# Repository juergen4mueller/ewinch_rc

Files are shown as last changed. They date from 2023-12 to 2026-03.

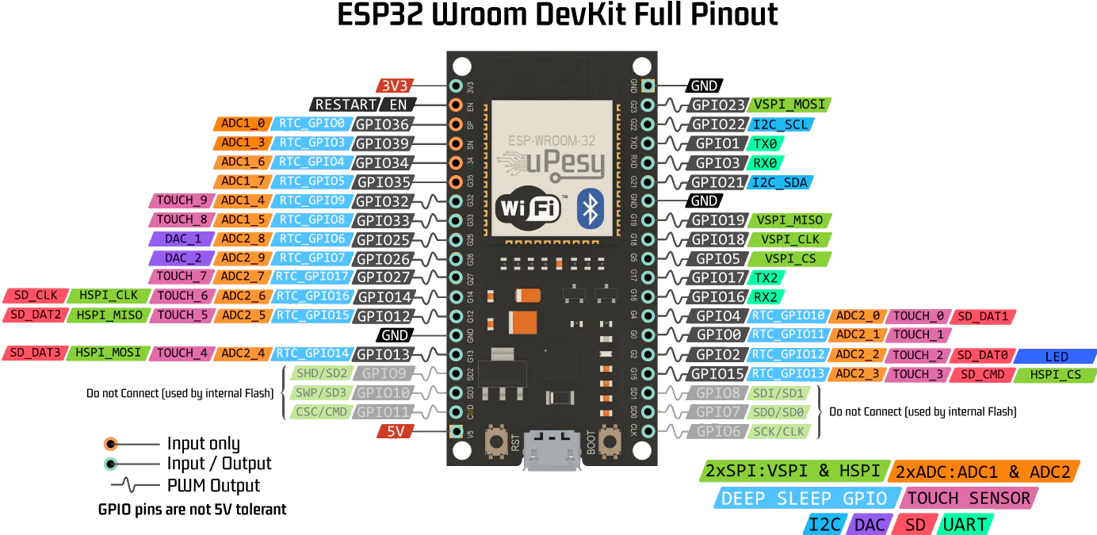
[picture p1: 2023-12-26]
doc/ESP32_38_Pinout.png

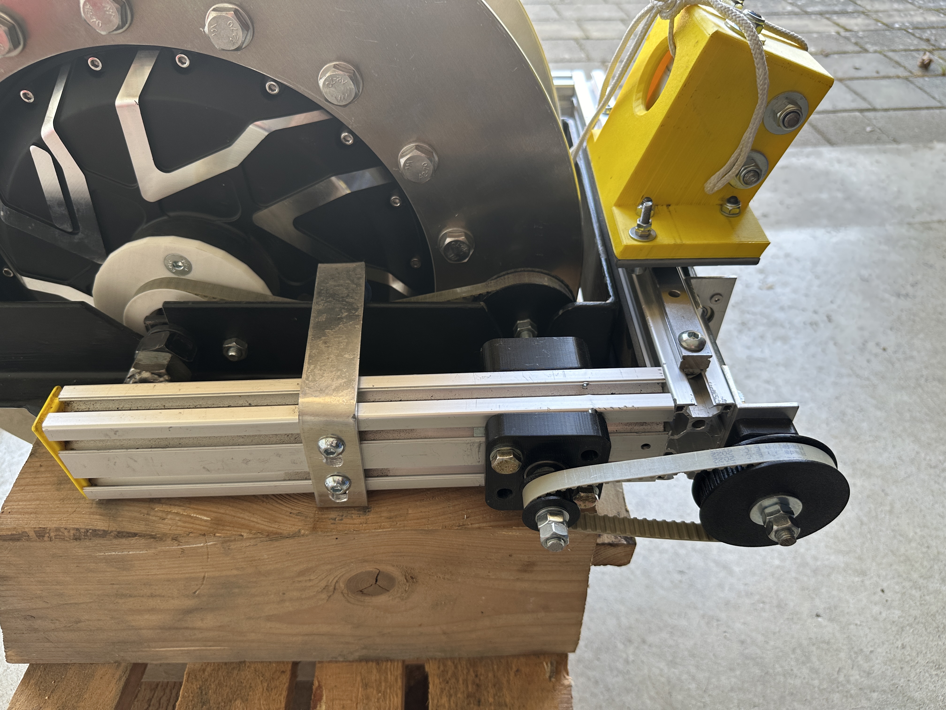
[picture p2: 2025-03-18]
doc/IMG_1781 2.JPG

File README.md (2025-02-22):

# ewinch_remote_controller
 transmitter and receiver code for remote controlling a paragliding winch
 forked from robertzach/ewinch_remote_controller

receiver uses PPM for driving the winch and (optinal) UART to read additional information (line length, battery %, dutycycle)
VESC UART communication depends on https://github.com/SolidGeek/VescUart/

Line auto stop can be implemented within VESC with vesc_ppm_auto_stop.patch
Default VESC app config is vesc_app_config.xml

## Changes / Updates
 Changed ESP32-Board to custom made with MH-ET-ESP32-Devkit and Heltec ESP32-Lora(v3).
 chandrawi/LoRaRF-lib for usage of SX126x modul on Heltec v3.
 Made new case for Heltec module, same size but different mount points.
 Moved software project to PLATFORMIO using VSCode for convenience work.

## Software improvements:
 - rotary encoder in transmitter to adjust max. weight, default pull and transmitter id (push while switch on, then select and push to confirm)
 - EEPROM function in transmitter to hold last "max. weight" value.
 - rotary encoder in receiver used to pull manually (adjust force by turning, push stops immediately)

## work in progress
 - wind direction from winch transmitting to cockpit display
 - warning lamp if pull mode active
 - cutting system

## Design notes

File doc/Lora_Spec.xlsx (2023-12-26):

Sx1272 |  |  | Sx1262
Lora Packet
Preamble | Sync, 12 Symbol long, Length variable (RegPreambleMsb, RegPreambleLsb)
Header / CRC | Nur verwendet wenn RegModemConfig1:ImplicitHeaderModeOn gesetzt ist
Expl. Header Mode | Ist default mode: Payload Length, ECCR, CRC?
Impl. Header Mode | Wenn SF (spreading factor) == 6 nur impl. Header mode möglich
Payload | Daten
CRC
Spreading Factor | RegModemConfig2 (6 für highest data rate)
Coding Rate | RegModemConfig1
Bandwidth
Mode | RXCONTINUOUS
SyncWord | default: 0xF5 | MSB:0x14, LSB:0x24
PreambleSize | def: 0x00
RegOpMode(0x01) | def:0x00 LoRa:0x80 , ModeSTBY:0x01, ModeTX:0x03, ModeRXSINGLE:0x6, ModeRXCONTINUOUS:0x5
RegModemConfig1(0x1D) | Bandwidth, CodingRate, ImplHeaderMode, RxPayloadCrcOn, LowDataRateOptimize
RegModemConfig2(0x1E) | SpreadingFaktor, TxContinuousMode, AgcAutoOn, SymbTimeout
RxGain |  | 0x94(PowerSaving), 0x96(Boost)
 |  | BUSY-Line: If Busy == 0, state machine waits for command
 |  | BUSY geht auch high wenn ein IRQ kommt. Dann erst die Daten lesen wenn BUSY wieder low ist
Packet Filtering based on preamble start

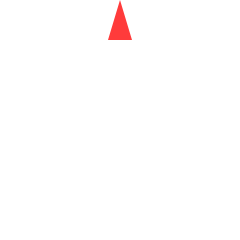
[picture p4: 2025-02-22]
assets/WindPfeil_2.png

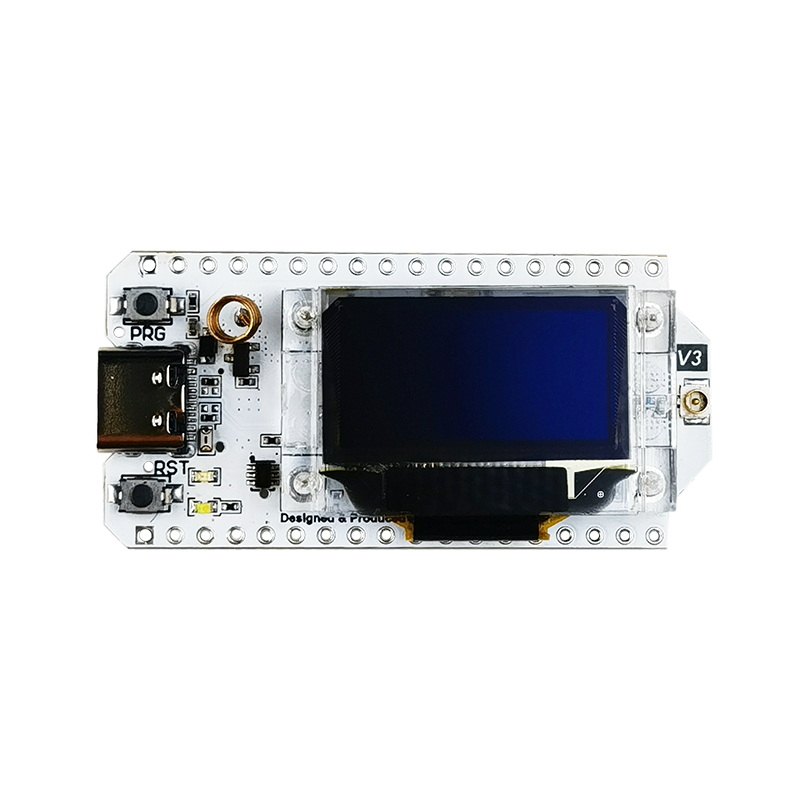
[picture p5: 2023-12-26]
doc/LORA32-V3vt.png

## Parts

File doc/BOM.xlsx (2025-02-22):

Bauteilliste Winde
QS Motors | 979.00 € | +Steuer
MakerX Go FOC G300 | 350.00 €
Trommelscheiben (Lasercut) | 150.00 €
Schrauben M12x150 + Muttern/Scheiben | 60.00 €
Stahlwinkel 80x80x6 | 16.14 €
Stahlwinkel 60x30x5 2m | 14.82 €
Stahlrohr 33,7x2,5 | 3.60 €
Stahlrohr 42,4x3,2 | 5.40 €
Alu-Rohr 30x2 | 11.79 €
Kugellager 10x26x8 | 7.90 €
Mutter M22x1,5 5St. | 8.45 €
Item 30x60 500mm 4St | 36.40 €
Kugellager 8x22x7mm | 10.00 €
Klappstecker 8x50mm | 10.00 €
Lenkungsdämpfer einstellbar | 150.00 €
Schleppseil 1040m 2,5mm | 345.00 €
Gewindestange M8
Alu-Winkel 30x30x3mm
Zahnriemen 10-T5/630 | 16.97 €
Zahnriemen 10-T5/350 | 16.20 €
Seilfallschirm
Sollbruchstelle
AliExpress
ESP32 SX1262 2x | 36.90 €
280x240x130mm Werkzeug kasten | 17.35 € | https://de.aliexpress.com/item/1005005539521602.html
Taster für Remote | 5.00 € | https://de.aliexpress.com/item/1005003256497233.html
Linearführung MGN15 H, China, 300mm | 16.86 € | https://de.aliexpress.com/item/32806622073.html
ESP32 Dev Modul 38P | 3.28 € | https://de.aliexpress.com/item/1005001636295529.html
KFL000 10mm Lager |  | https://de.aliexpress.com/item/1005002394517514.html
1,28" Display Remote | 17.00 € | https://www.waveshare.com/esp32-s3-lcd-1.28.htm
LiPo-Akkus LP603449 1100 mAh | 20.00 €
Diverse Schrauben …
Item-Nutensteine
3D-Druck-Teile
Lagersitz
Akku 72V/30Ah | 1000.00 €
Gesamtkosten | 3308.06 €

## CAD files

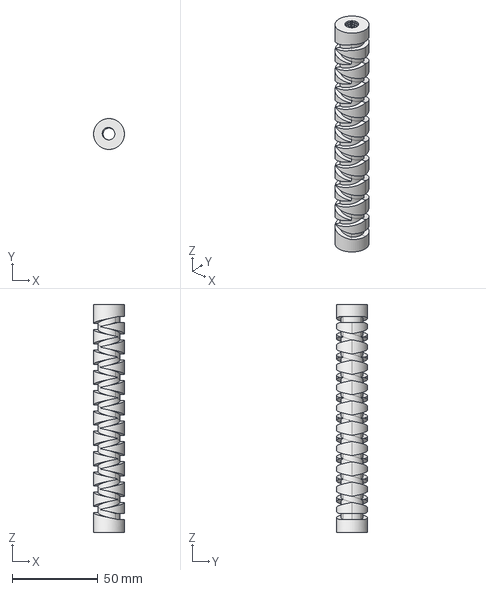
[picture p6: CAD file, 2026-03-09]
CAD/Kreuzspindel_kurz.step
18.0 x 18.0 x 133.0 mm

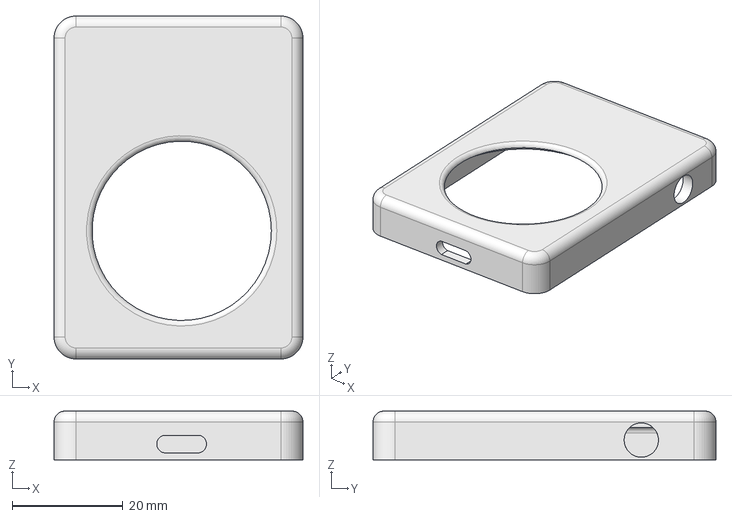
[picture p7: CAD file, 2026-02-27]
CockpitDisplay/DisplayCaseFront.step
45.0 x 62.0 x 8.85 mm

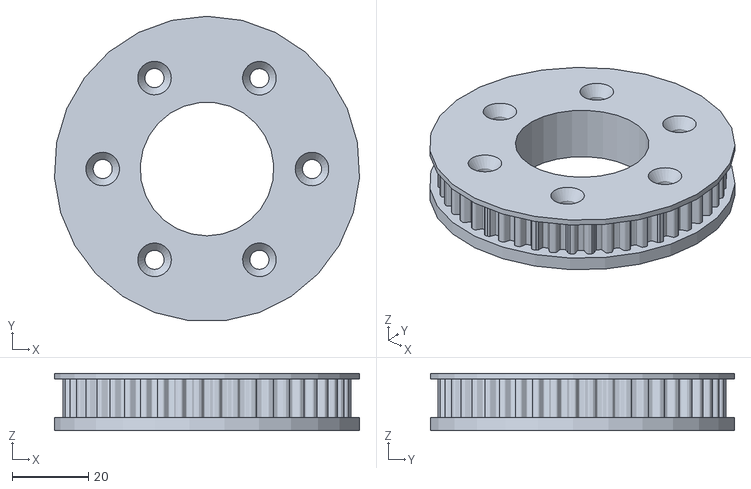
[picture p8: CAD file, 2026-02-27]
stl/belt_drive_B.stl
79.9 x 79.7 x 15.0

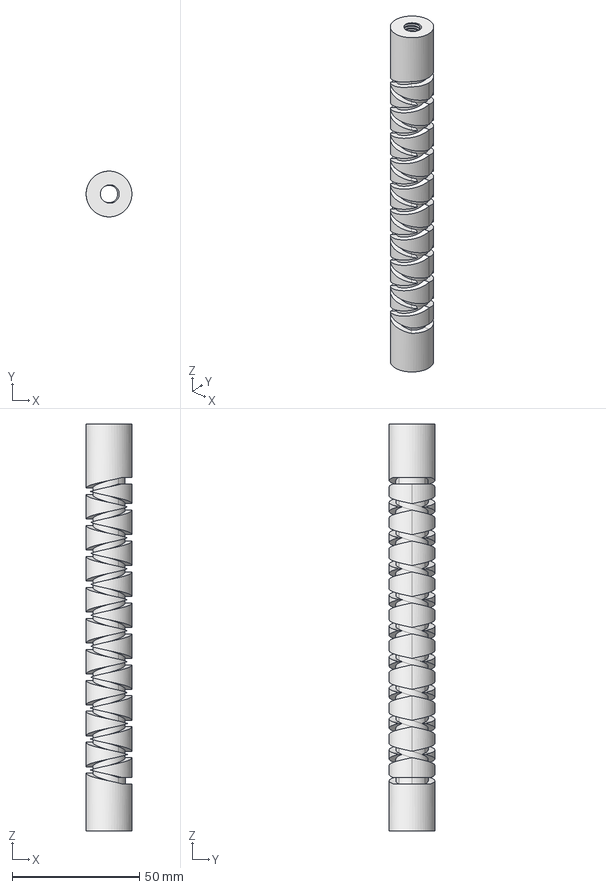
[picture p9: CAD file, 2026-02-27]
CAD/Kreuzspindel-slim_2.6_tief_10Gang.step
18.0 x 18.0 x 160.0 mm

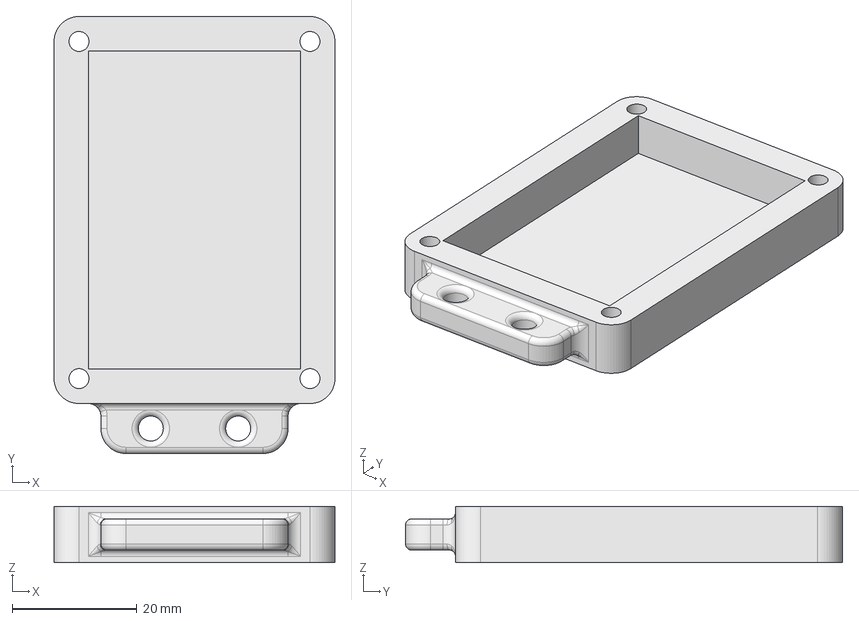
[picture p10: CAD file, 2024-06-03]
CockpitDisplay/DisplayCaseBack.step
45.0 x 70.0 x 9.00 mm

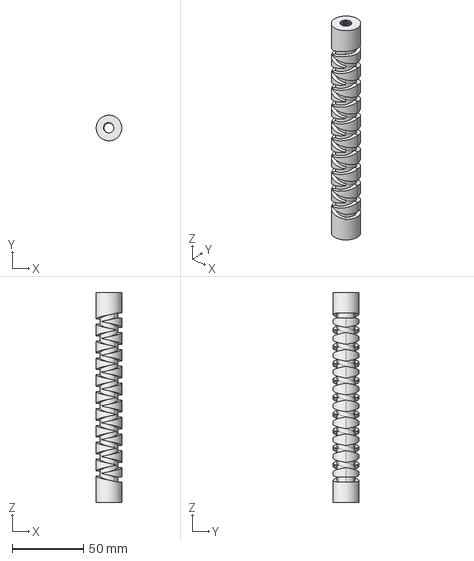
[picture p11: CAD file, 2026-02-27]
doc/CAD/Kreuzspindel_v2.step
18.0 x 18.0 x 147.5 mm

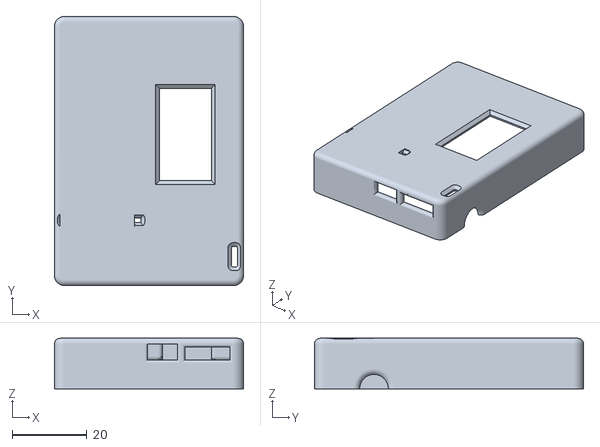
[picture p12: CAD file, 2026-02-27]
stl/transmitter_top.stl
50.6 x 71.9 x 13.5

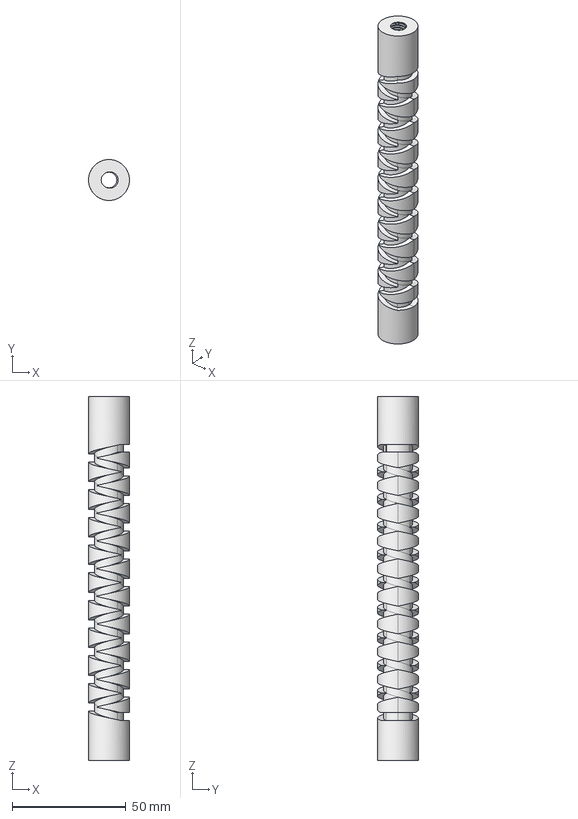
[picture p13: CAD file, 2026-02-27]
CAD/Kreuzspindel-Spindel_2.6_tief_10Gang.step
18.0 x 18.0 x 160.0 mm

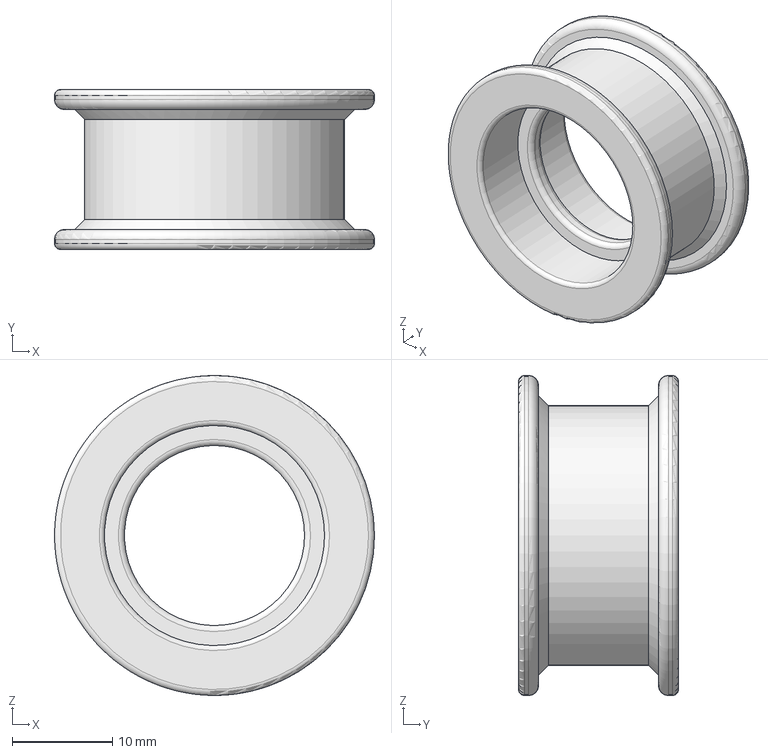
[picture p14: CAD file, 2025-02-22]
doc/CAD/Riemenspanner_Rolle.step
32.0 x 16.0 x 32.0 mm

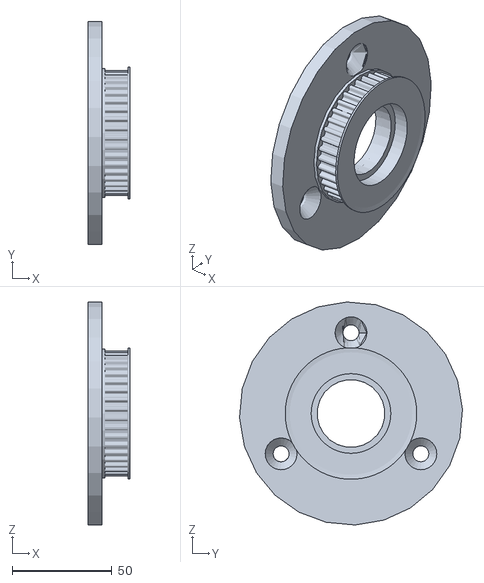
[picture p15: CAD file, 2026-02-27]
stl/belt_drive_A.stl
21.3 x 111.9 x 111.9

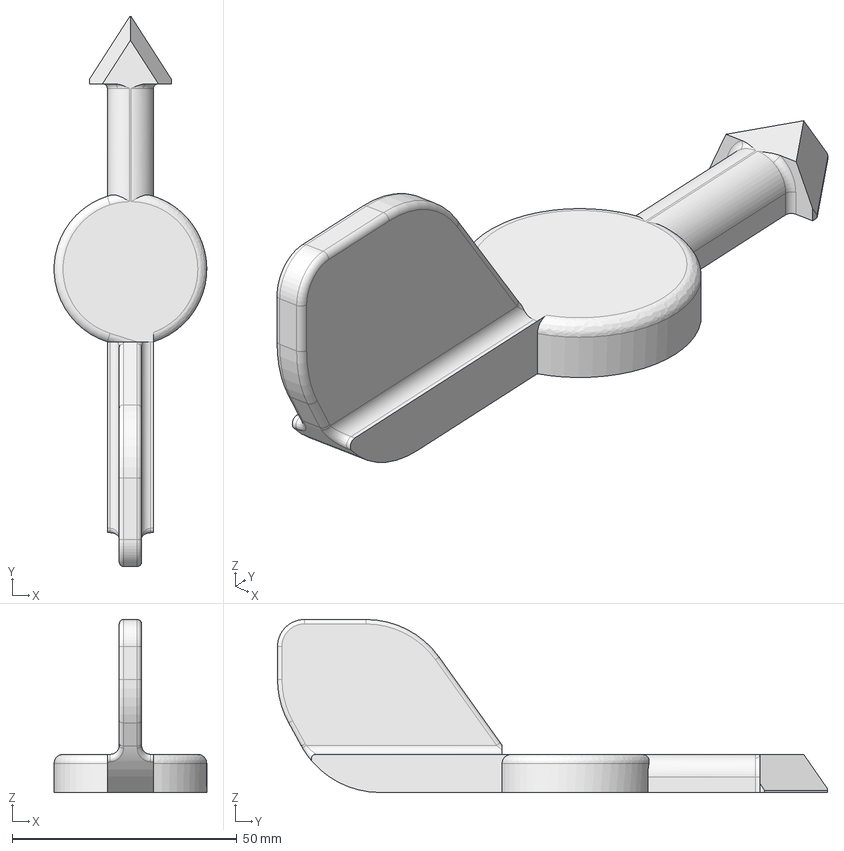
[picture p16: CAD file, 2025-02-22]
CAD/Windmesser.FCStd
34.0 x 122.4 x 38.5 mm

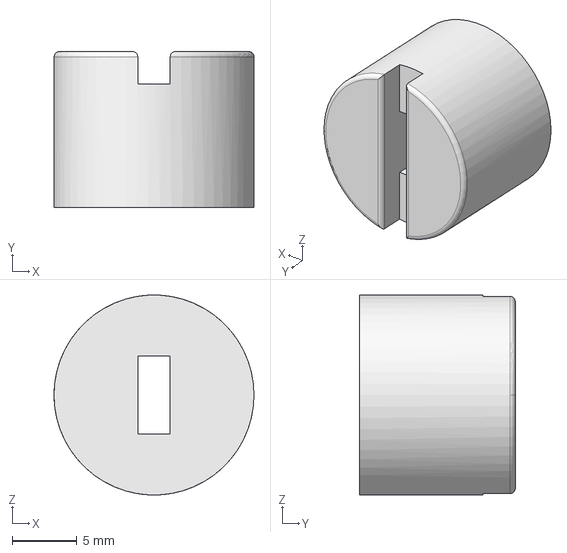
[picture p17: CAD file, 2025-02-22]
doc/CAD/Schleifersitz_Kreuzspindel.step
15.4 x 12.0 x 15.4 mm

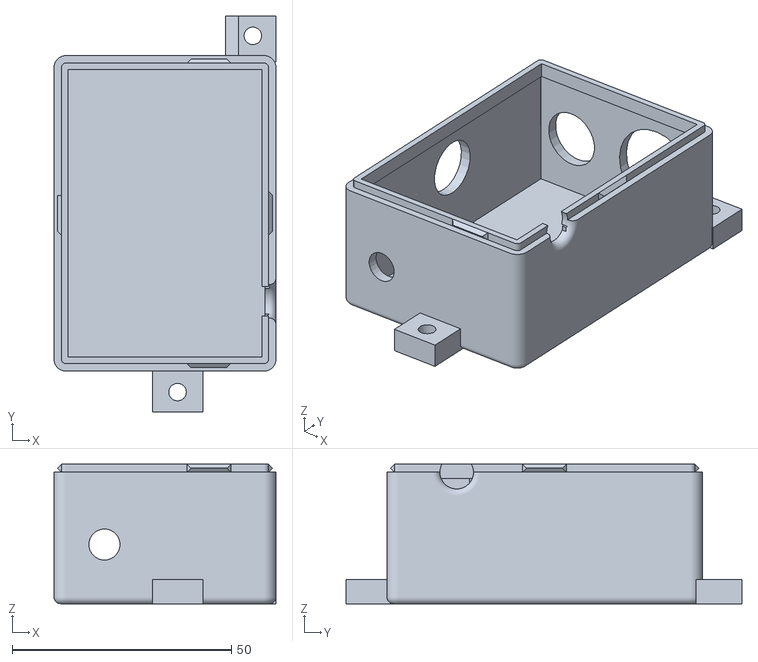
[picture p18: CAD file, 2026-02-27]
stl/transmitter_bottom.stl
50.6 x 90.2 x 31.8

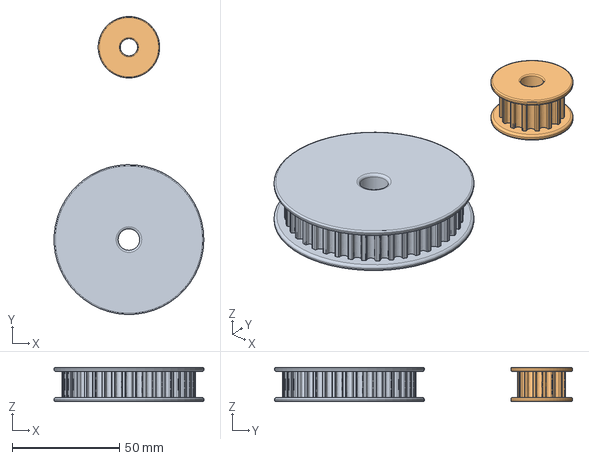
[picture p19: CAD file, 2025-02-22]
CAD/Riemenscheiben.FCStd
69.9 x 139.1 x 16.0 mm
40Z
15Z

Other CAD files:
doc/CAD/Remote_Display_Front.step
doc/CAD/Halter_Lagersitz_Spulvorrichtung.step
stl/TransmitterCaseHeltec_btm.stl
CAD/Halter_Spuler-Schablone.step
CAD/Halter_Spuler-Schablone2.step
CAD/Halter_Spuler.FCStd
CAD/LagerUmsetzer.FCStd
CAD/Riemenscheibe_40Z.FCStd
CAD/TransmCaseHeltec.FCStd
CAD/Trommelblatt_5mm_Alu.dxf
CAD/Winde_Trommelblatt.FCStd
doc/CAD/Gleiter_Kreuzspindel.step
doc/CAD/Gleiteradapter_Kreuzspindel.step
doc/CAD/LagerUmsetzer-Aussen15mm.step
doc/CAD/LagerUmsetzer-Innen25mm.step
doc/CAD/Lagersitz_Spulvorrichtung.step
doc/CAD/Remote_Display_Back.step
doc/CAD/Riemenscheibe_15Z.step
doc/CAD/Riemenscheibe_40Z.step
doc/CAD/Schleifer_Kreuzspindel.step
doc/CAD/Trommelblatt.step
doc/CAD/Trommelblatt_5mm_Alu.dxf
stl/TransmitterCaseHeltec_top.stl

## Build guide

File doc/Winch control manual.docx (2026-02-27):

Winch control manual

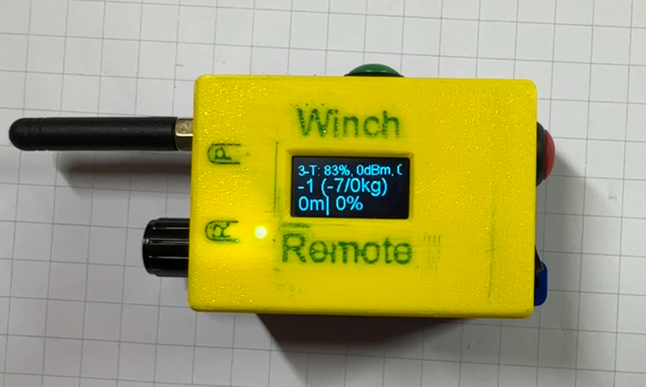
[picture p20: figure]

BTN UP

BTN DOWN

Setup Switch

Lora Antenna

Switch

ON / OFF

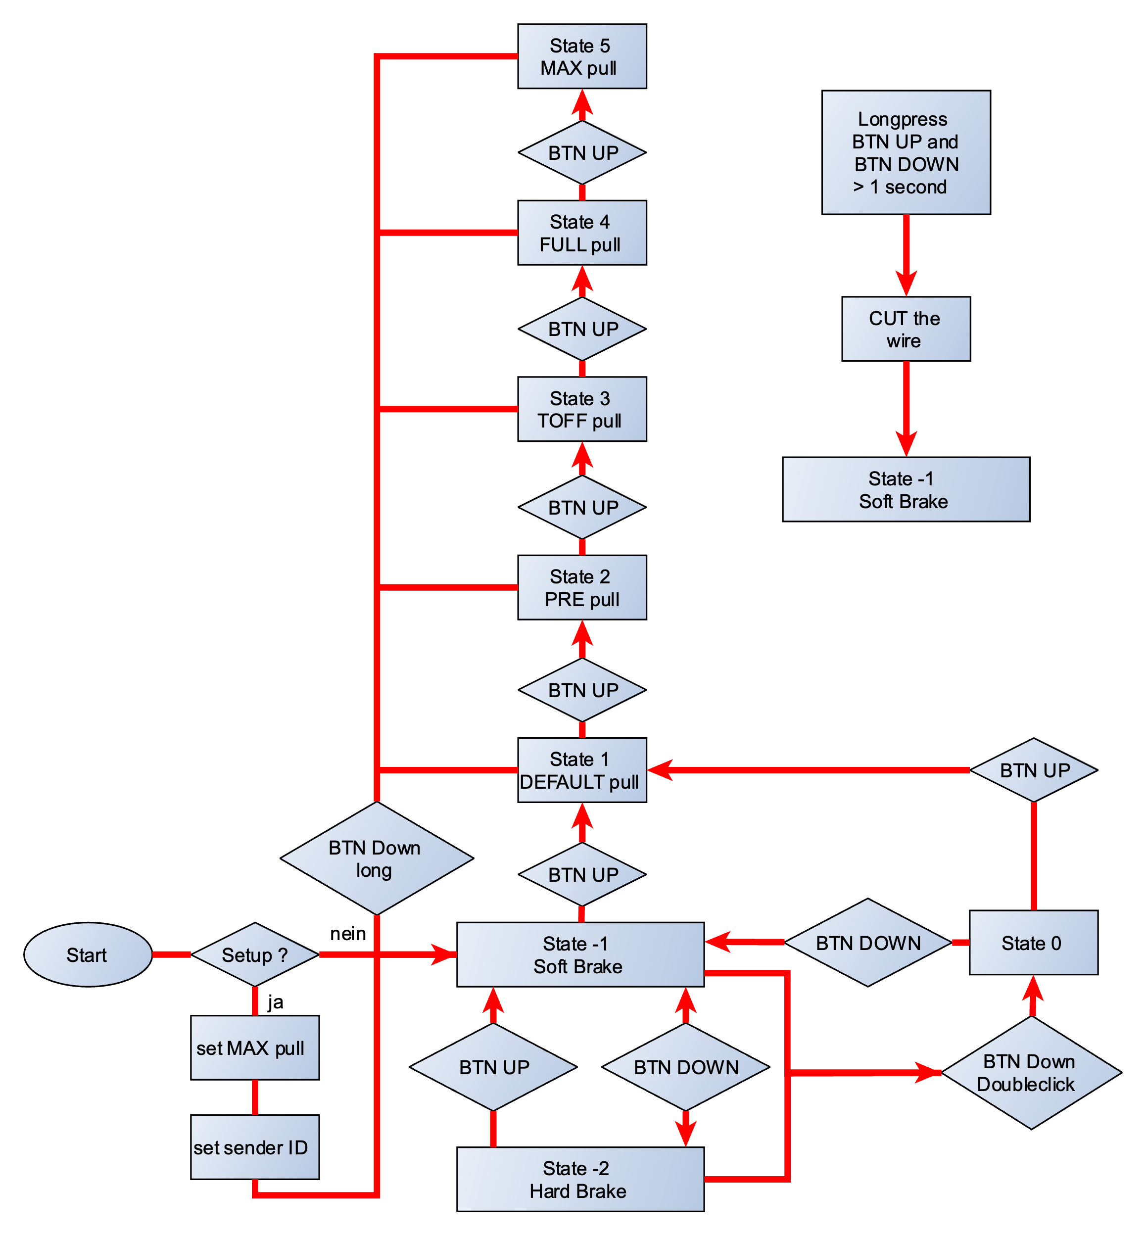
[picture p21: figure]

Remote Display

Due to the fact that the display on the remote control is hard to read while towing I made a display connected by ESP-NOW to the remote control.

This can be attached to the cockpit and is easy to read.

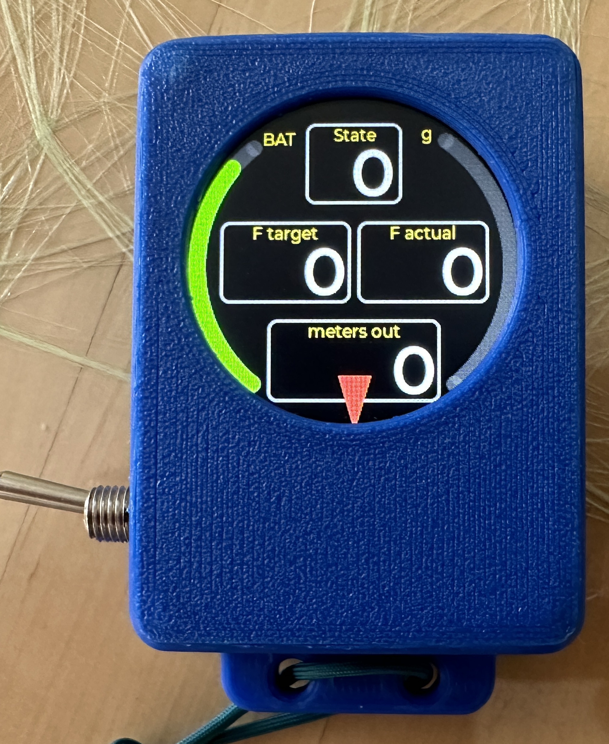
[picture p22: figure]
Remote Display Extention

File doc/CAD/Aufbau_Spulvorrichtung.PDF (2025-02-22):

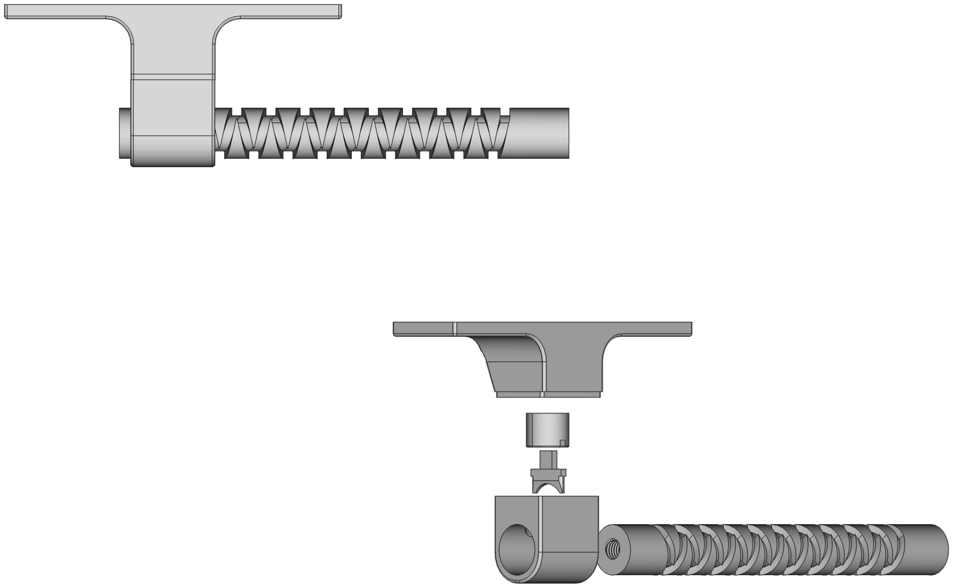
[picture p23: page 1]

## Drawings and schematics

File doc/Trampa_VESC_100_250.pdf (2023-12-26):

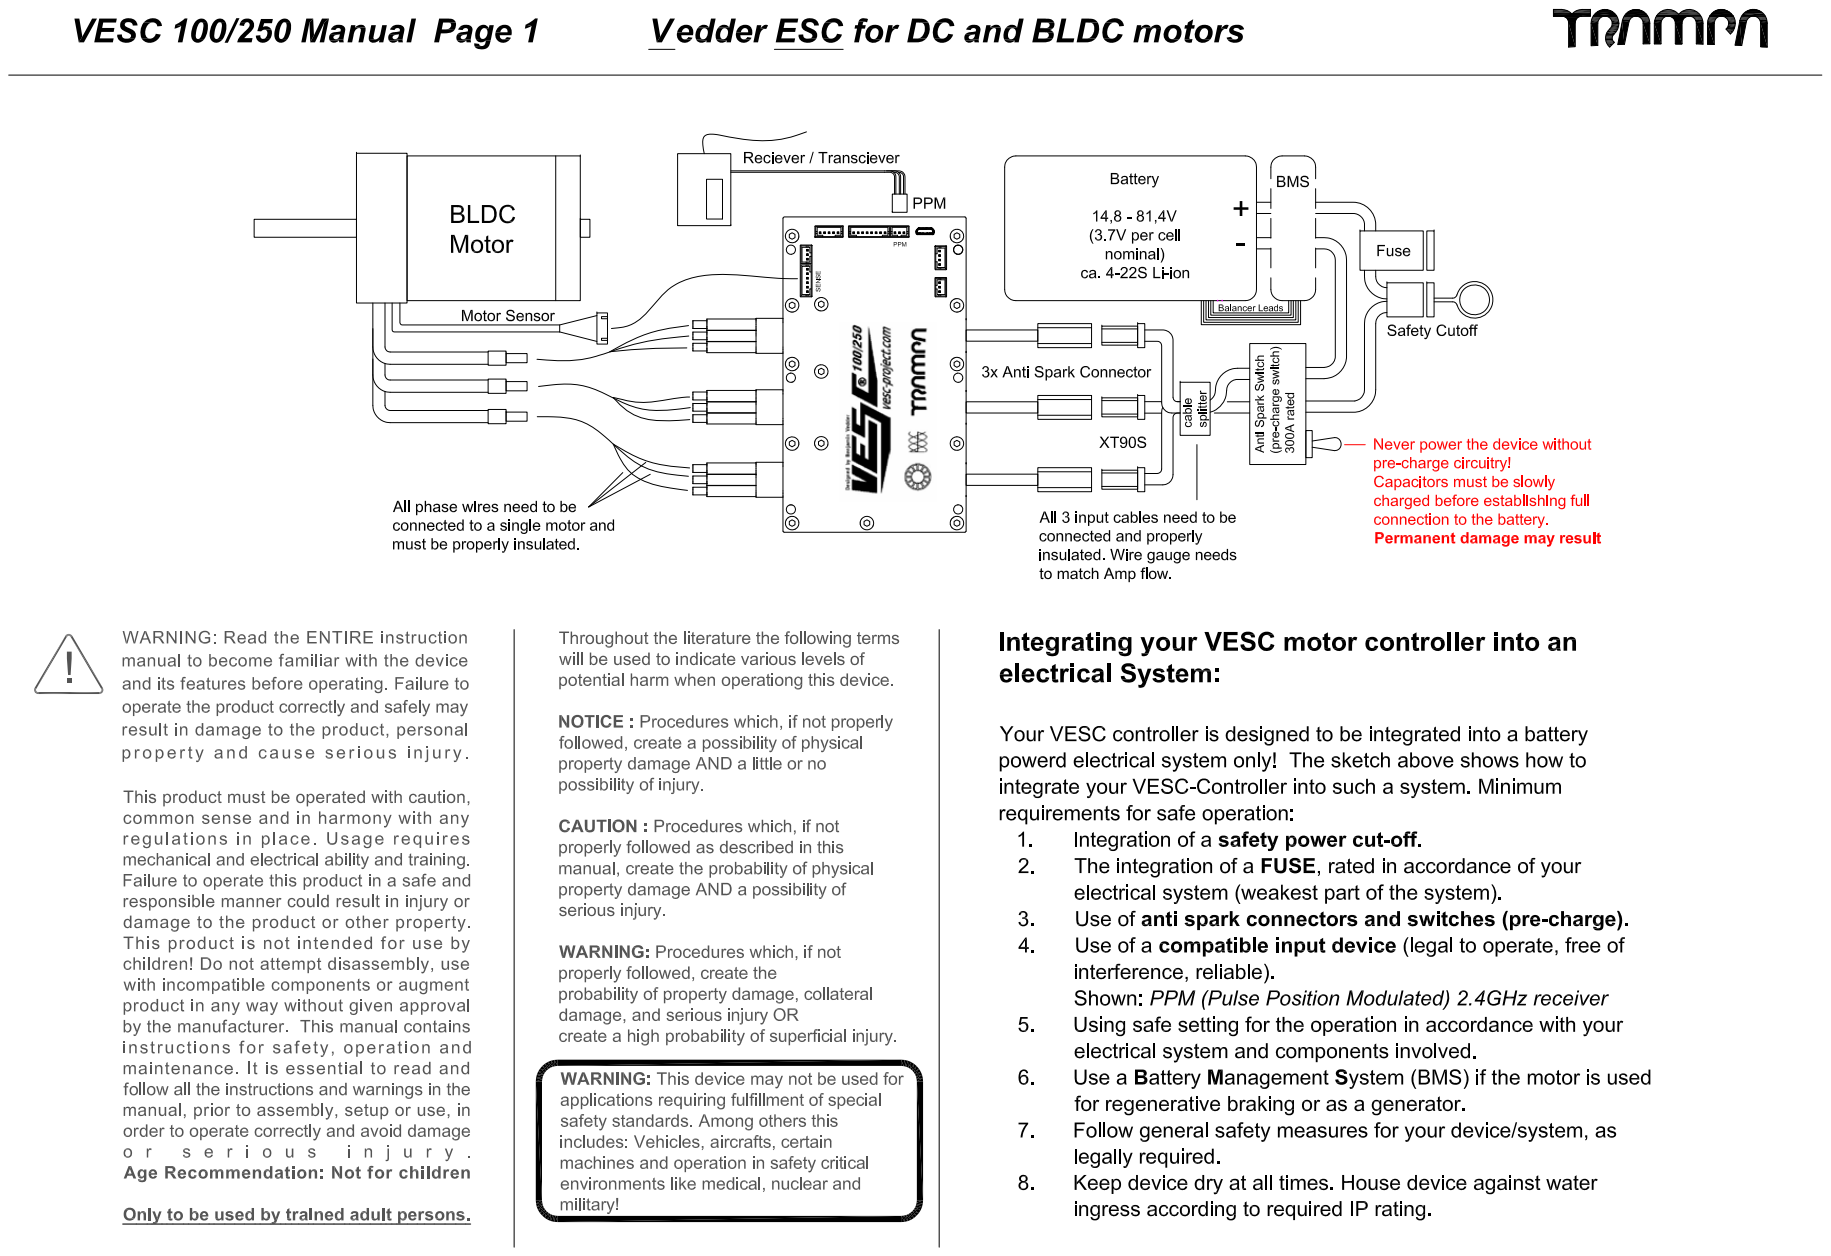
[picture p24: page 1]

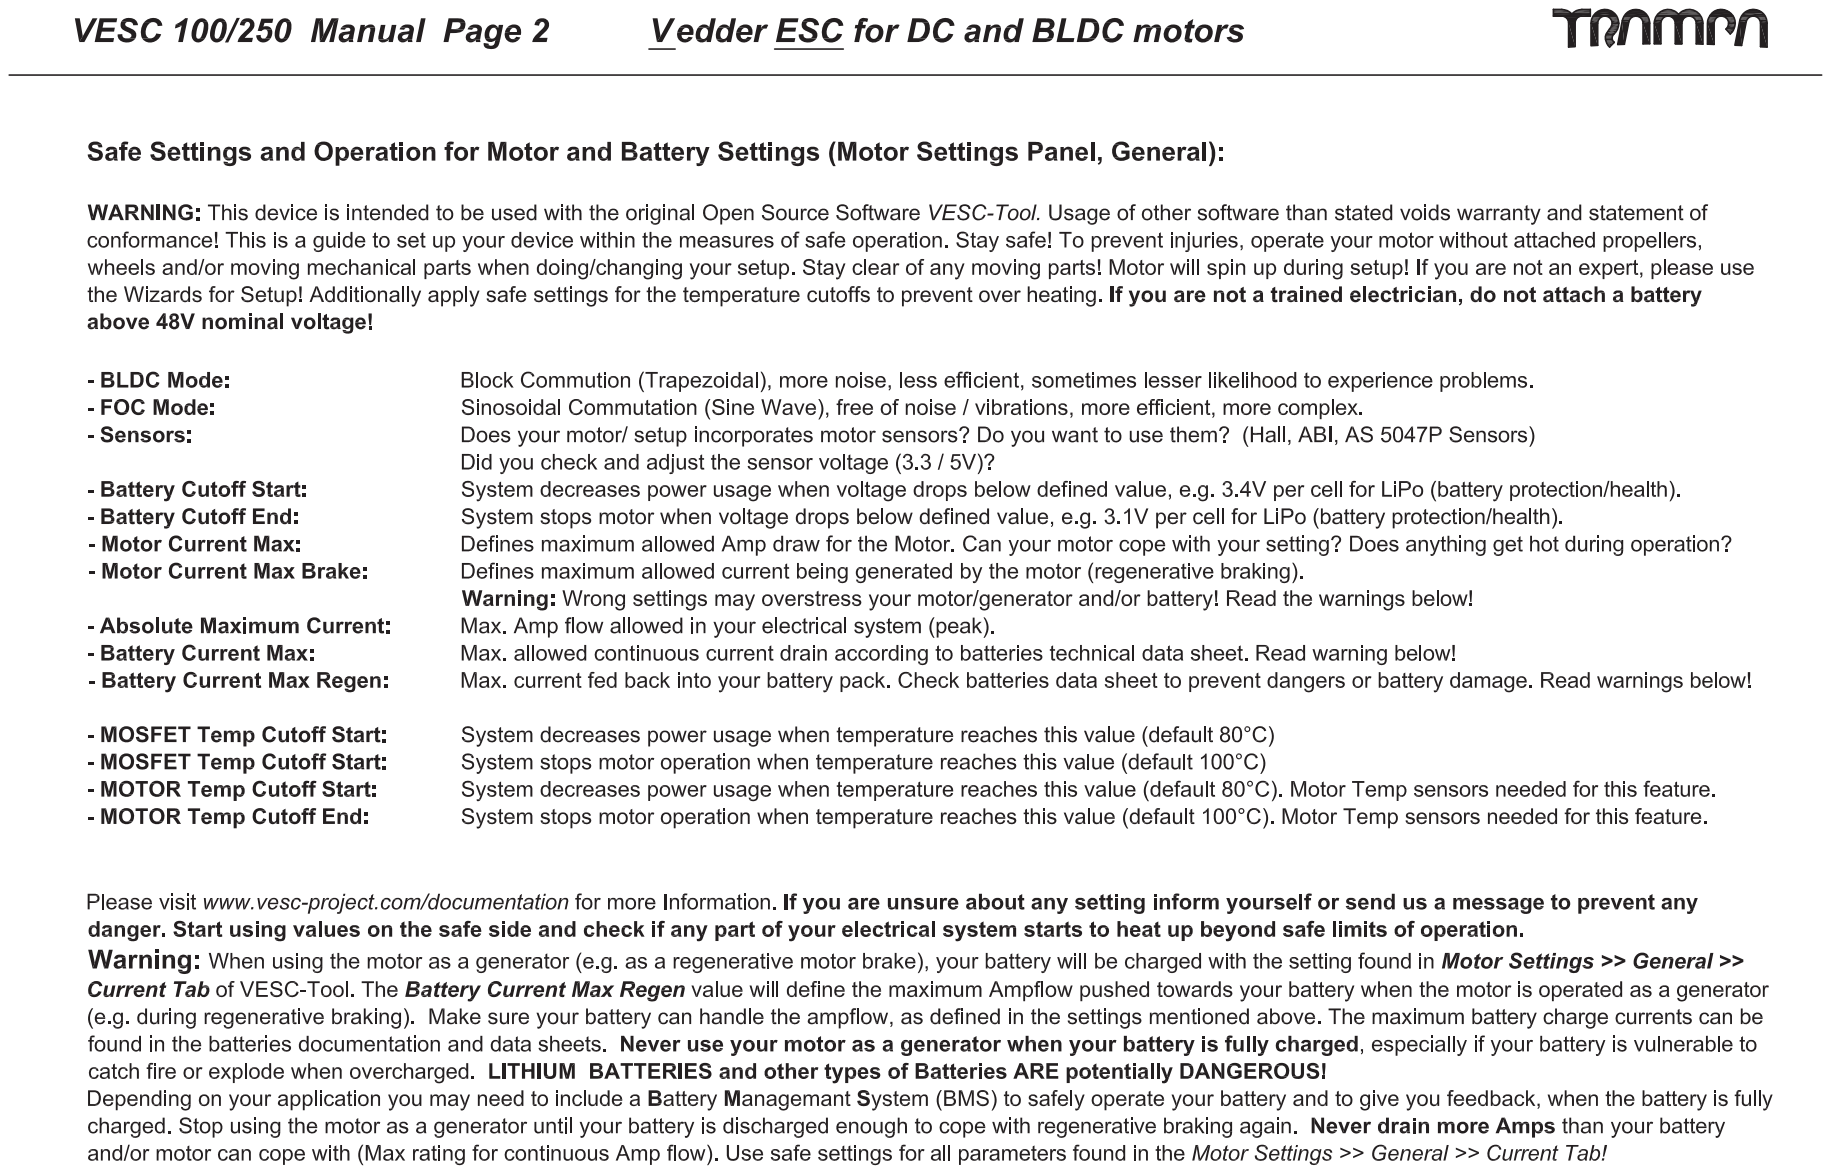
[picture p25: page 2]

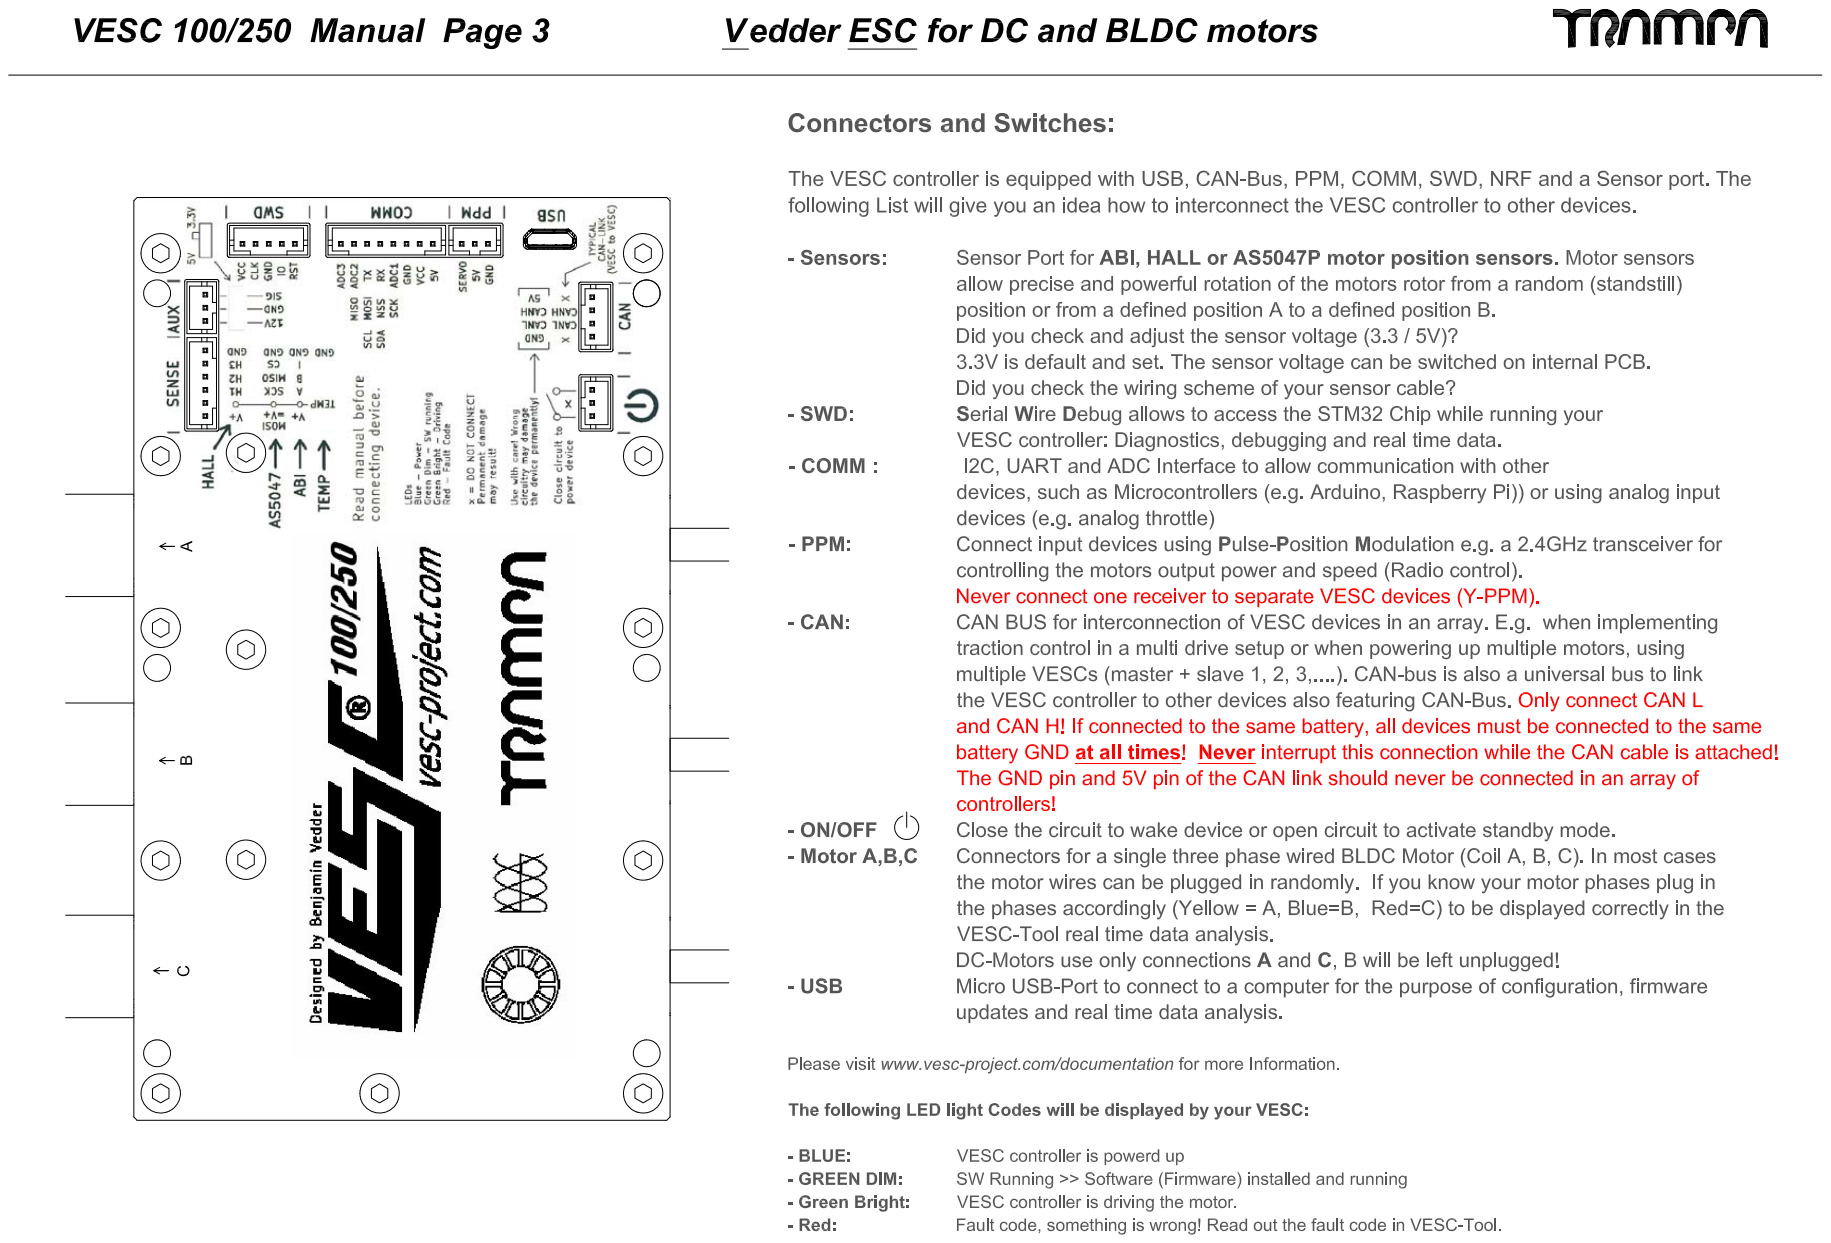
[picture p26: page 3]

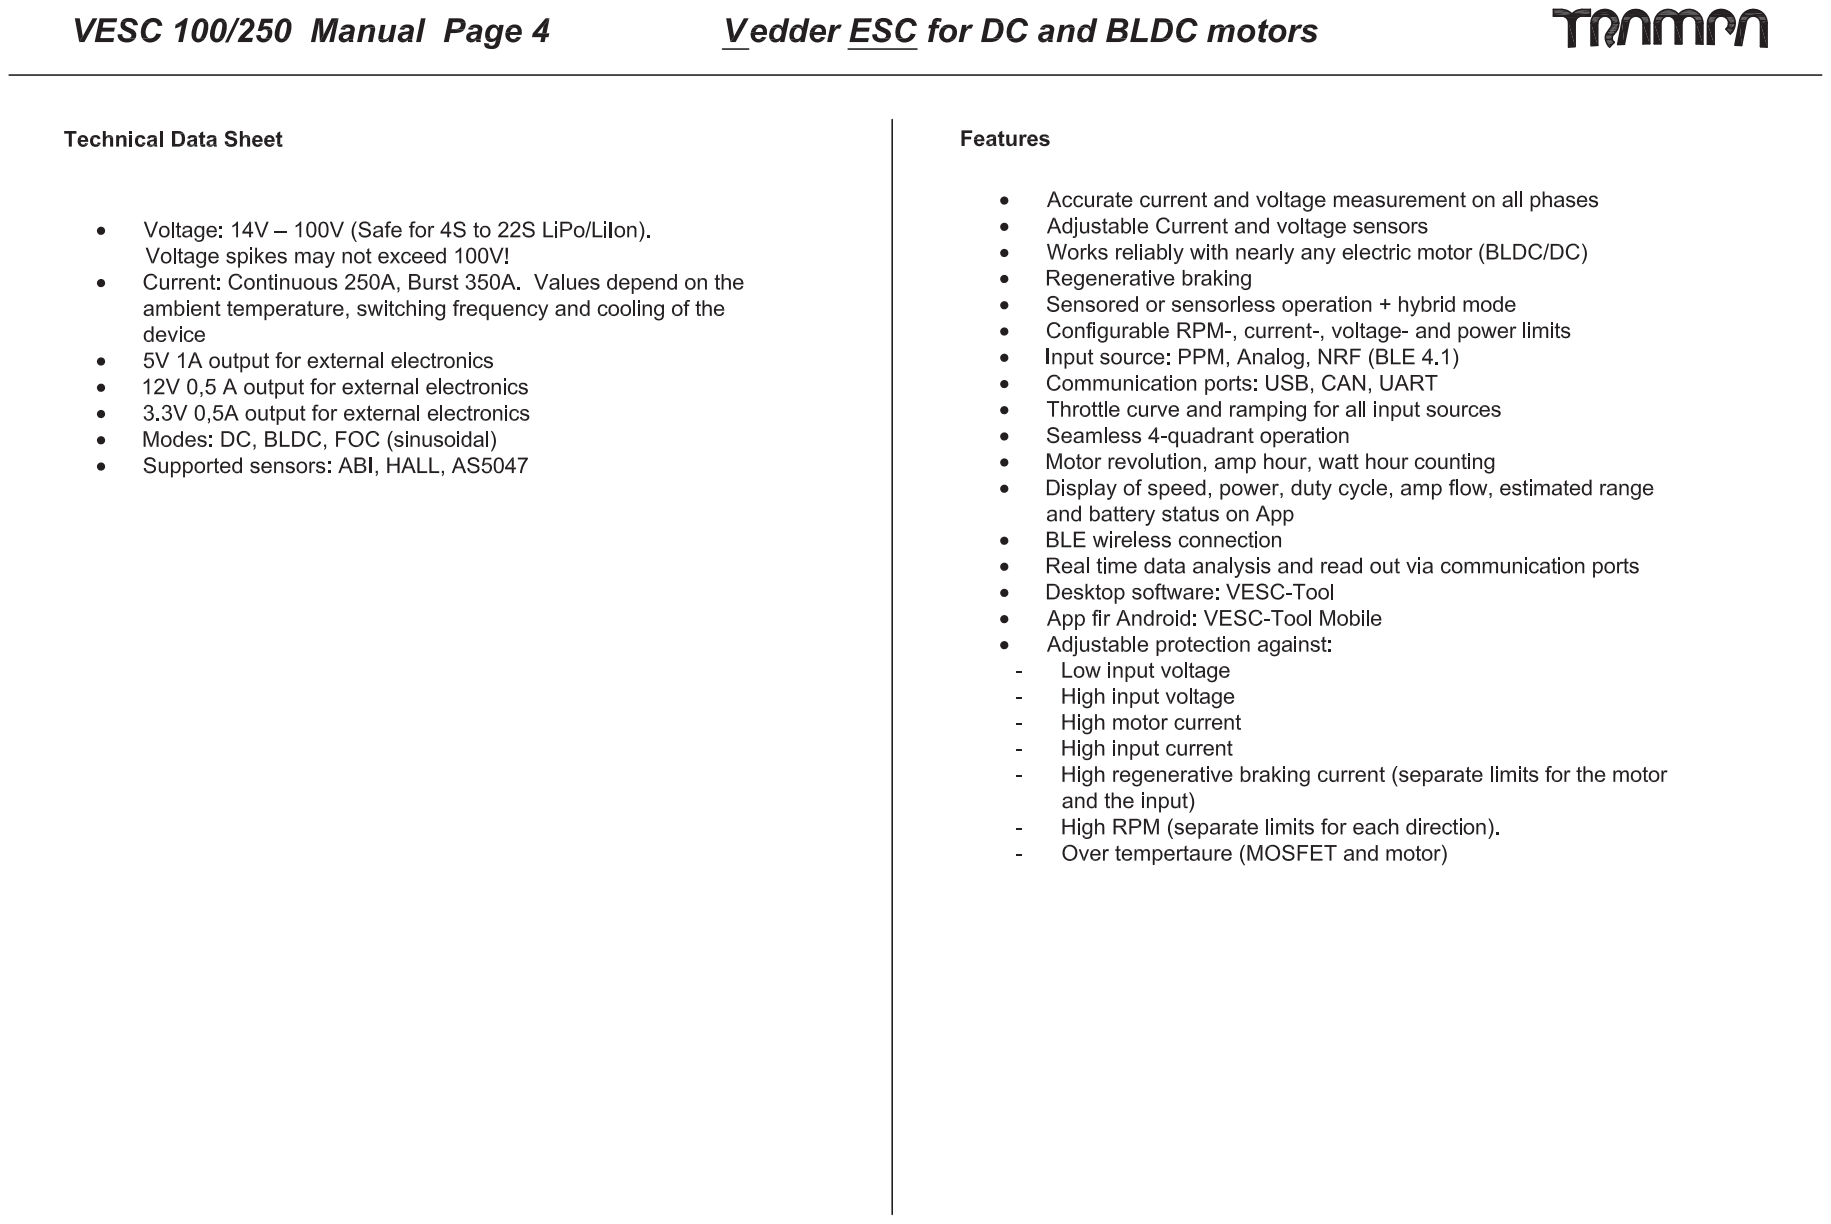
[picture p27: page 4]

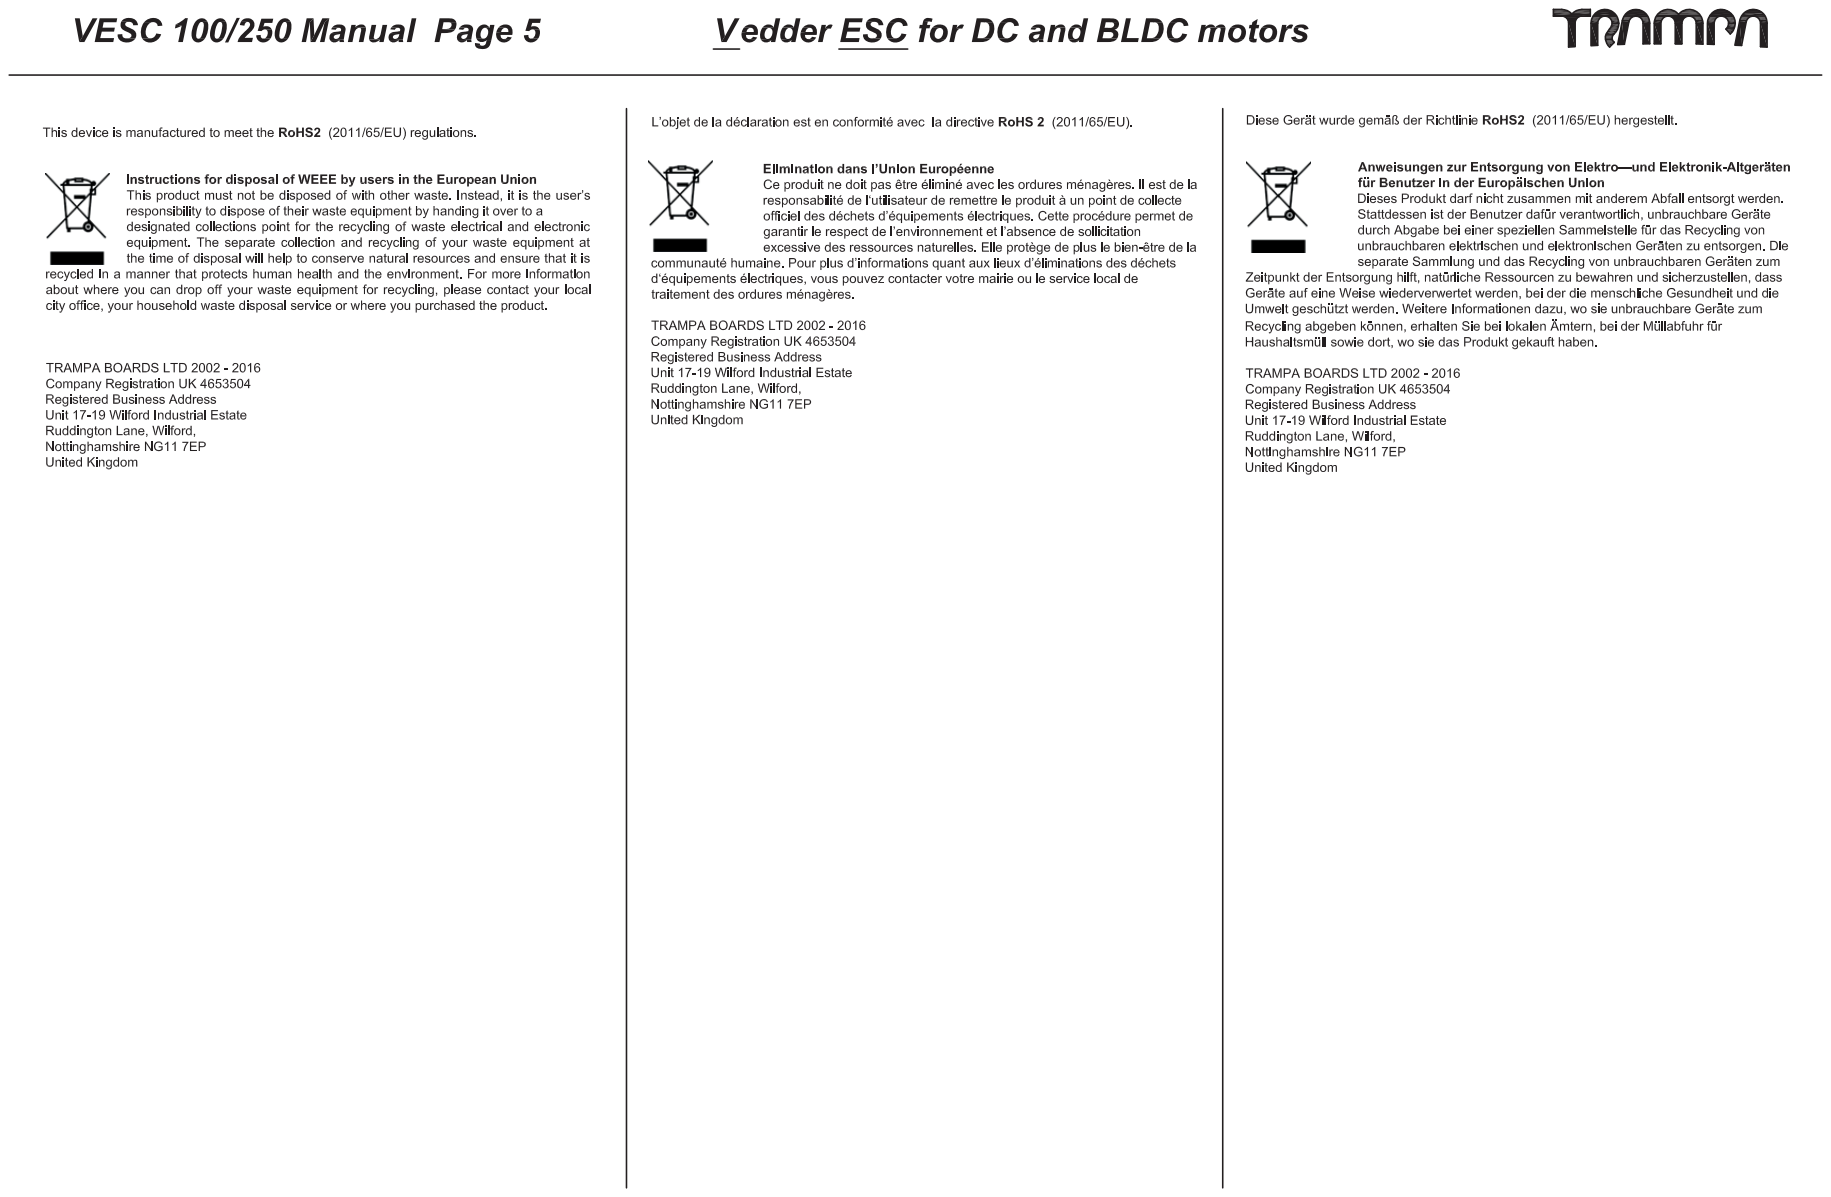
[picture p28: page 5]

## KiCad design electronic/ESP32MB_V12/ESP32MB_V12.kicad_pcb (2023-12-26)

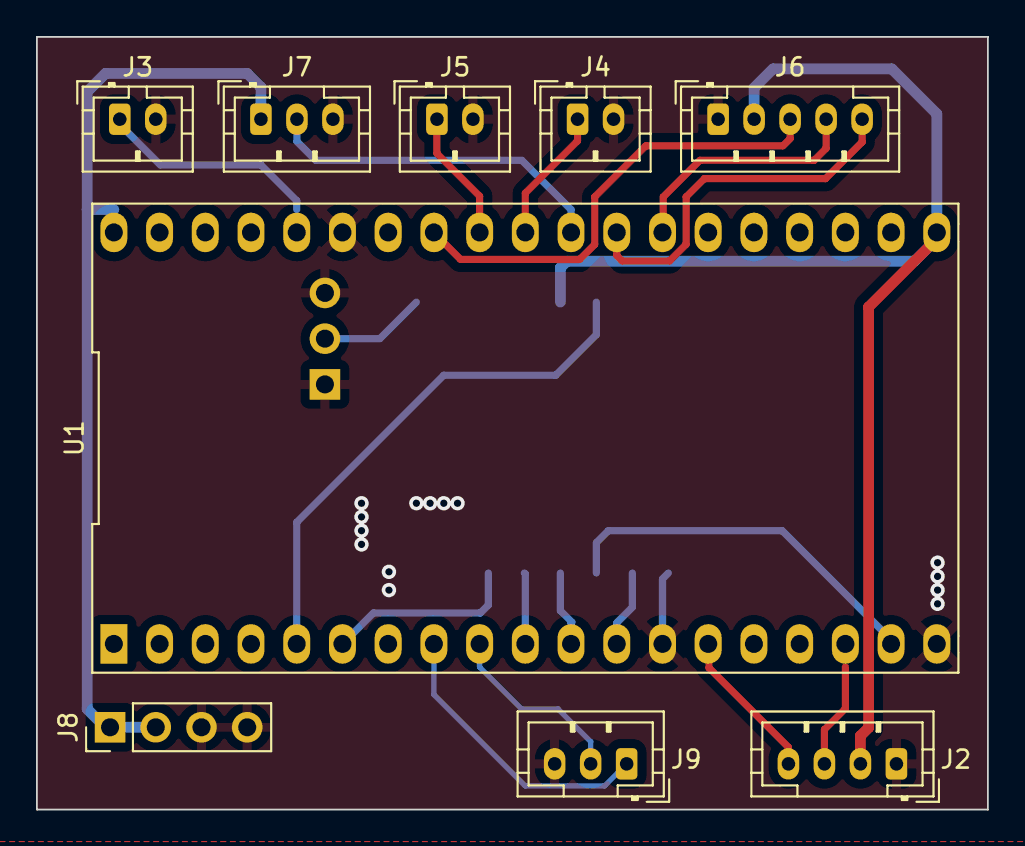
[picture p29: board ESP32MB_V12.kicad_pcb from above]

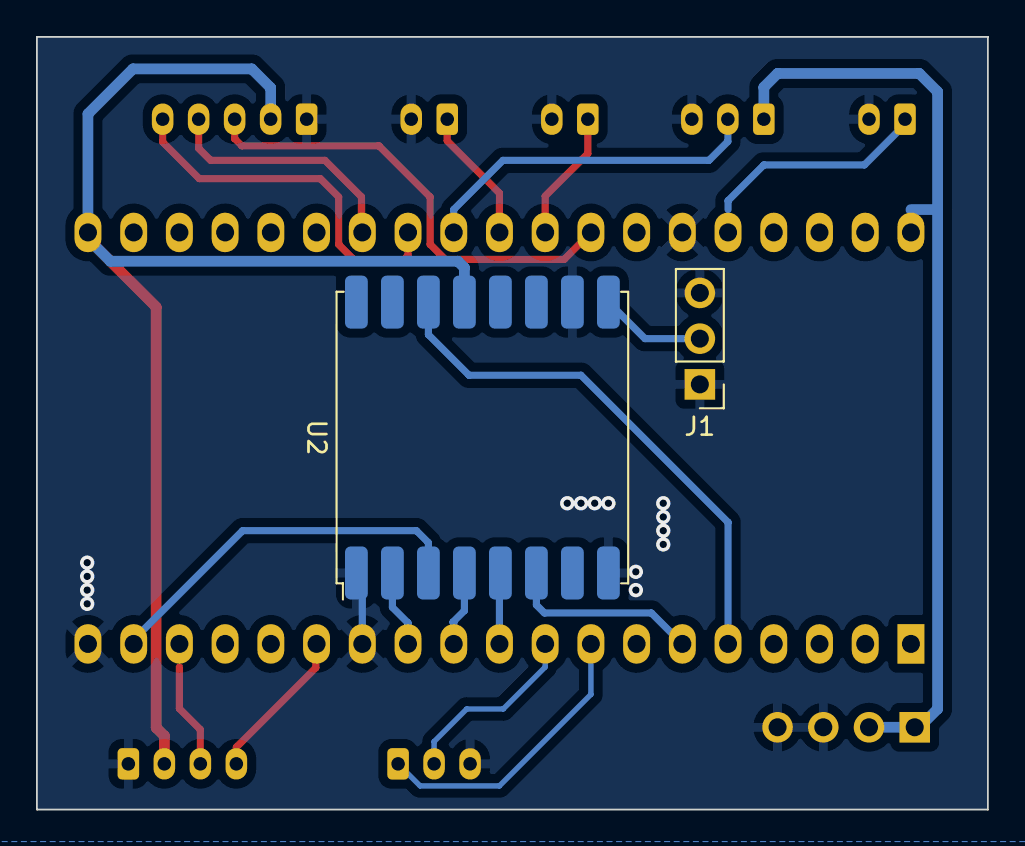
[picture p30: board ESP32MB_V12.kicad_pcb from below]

Board: 2 copper layers, 52.8 x 42.9 mm, 11 parts (2 on the bottom side), 21 nets.

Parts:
J1: Conn_01x03_Socket; PinHeader_1x03_P2.54mm_Vertical
J2: Conn_01x04_Pin; JST_PH_B4B-PH-K_1x04_P2.00mm_Vertical
J3: VESC_PWM; JST_PH_B2B-PH-K_1x02_P2.00mm_Vertical
J4: BTN_UP; JST_PH_B2B-PH-K_1x02_P2.00mm_Vertical
J5: BTN_DOWN; JST_PH_B2B-PH-K_1x02_P2.00mm_Vertical
J6: Conn_01x05_Pin; JST_PH_B5B-PH-K_1x05_P2.00mm_Vertical
J7, J9: Conn_01x03_Pin; JST_PH_B3B-PH-K_1x03_P2.00mm_Vertical
J8: Conn_01x04_Pin; PinHeader_1x04_P2.54mm_Vertical
U1: MH-ET-ESP32-DEVKIT; MH-ET-ESP32-Devkit_small
U2: RFM95W-868S2; HOPERF_RFM9XW_SMD

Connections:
3V3: J2.2, J6.2, U1.20 (3V3), U2.13 (3.3V)
5V: J7.1, J8.1, J8.2, U1.38 (5V)
Audio: J7.2, U1.28 (GPIO_25)
BTN_DOWN: J5.1, U1.30 (GPIO_27)
BTN_UP: J4.1, U1.29 (GPIO_26)
GND: J1.1, J1.3, J2.1, J3.2, J4.2, J5.2, J6.1, J7.3, J8.3, J8.4, J9.3, U1.13 (GND), U1.19 (GND), U1.33 (GND), U2.1 (GND), U2.8 (GND), U2.10 (GND)
LORA_CS: U1.10 (GPIO_5_VSPI_CS), U2.5 (NSS)
LORA_DIO0: U1.5 (GPIO_2_Touch_2), U2.14 (DIO0)
LORA_MISO: U1.12 (GPIO_19_VSPI_MISO), U2.2 (MISO)
LORA_MOSI: U1.18 (GPIO_23_VSPI_MOSI), U2.3 (MOSI)
LORA_RST: U1.6 (GPIO_0_Touch_1), U2.6 (RESET)
LORA_SCK: U1.11 (GPIO_18_VSPI_CLK), U2.4 (SCK)
unnamed: J1.2, U2.9 (ANT)
OLED_SCL: J2.3, U1.17 (GPIO_22_I2C_SCL)
OLED_SDA: J2.4, U1.14 (GPIO_21_I2C_SDA)
ROTARY_A: J6.4, U1.26 (ADC1_4_GPIO_32)
ROTARY_B: J6.5, U1.27 (ADC1_5_GPIO_33)
ROTARY_SW: J6.3, U1.31 (HSPI_CLK_GPIO_14)
VESC_PWM: J3.1, U1.34 (HSPI_MOSI_GPIO_13)
VESC_RX: J9.2, U1.9 (GPIO_17_TX2)
VESC_TX: J9.1, U1.8 (GPIO_16_RX2)

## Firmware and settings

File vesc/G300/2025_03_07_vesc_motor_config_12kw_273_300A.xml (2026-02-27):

<?xml version="1.0" encoding="UTF-8"?>
<MCConfiguration>
    <ConfigVersion>2</ConfigVersion>
    <pwm_mode>1</pwm_mode>
    <comm_mode>0</comm_mode>
    <motor_type>2</motor_type>
    <sensor_mode>0</sensor_mode>
    <l_current_max>350</l_current_max>
    <l_current_min>-250</l_current_min>
    <l_in_current_max>240</l_in_current_max>
    <l_in_current_min>-150</l_in_current_min>
    <l_abs_current_max>420</l_abs_current_max>
    <l_min_erpm>-100000</l_min_erpm>
    <l_max_erpm>100000</l_max_erpm>
    <l_erpm_start>0.8</l_erpm_start>
    <l_max_erpm_fbrake>300</l_max_erpm_fbrake>
    <l_max_erpm_fbrake_cc>1500</l_max_erpm_fbrake_cc>
    <l_min_vin>12</l_min_vin>
    <l_max_vin>96</l_max_vin>
    <l_battery_cut_start>40</l_battery_cut_start>
    <l_battery_cut_end>35</l_battery_cut_end>
    <l_slow_abs_current>0</l_slow_abs_current>
    <l_temp_fet_start>85</l_temp_fet_start>
    <l_temp_fet_end>100</l_temp_fet_end>
    <l_temp_motor_start>85</l_temp_motor_start>
    <l_temp_motor_end>100</l_temp_motor_end>
    <l_temp_accel_dec>0.15</l_temp_accel_dec>
    <l_min_duty>0.02</l_min_duty>
    <l_max_duty>0.95</l_max_duty>
    <l_watt_max>1.5e+06</l_watt_max>
    <l_watt_min>-1.5e+06</l_watt_min>
    <l_current_max_scale>1</l_current_max_scale>
    <l_current_min_scale>1</l_current_min_scale>
    <l_duty_start>1</l_duty_start>
    <sl_min_erpm>150</sl_min_erpm>
    <sl_min_erpm_cycle_int_limit>1100</sl_min_erpm_cycle_int_limit>
    <sl_max_fullbreak_current_dir_change>10</sl_max_fullbreak_current_dir_change>
    <sl_cycle_int_limit>62</sl_cycle_int_limit>
    <sl_phase_advance_at_br>0.8</sl_phase_advance_at_br>
    <sl_cycle_int_rpm_br>80000</sl_cycle_int_rpm_br>
    <sl_bemf_coupling_k>600</sl_bemf_coupling_k>
    <hall_table__0>-1</hall_table__0>
    <hall_table__1>1</hall_table__1>
    <hall_table__2>3</hall_table__2>
    <hall_table__3>2</hall_table__3>
    <hall_table__4>5</hall_table__4>
    <hall_table__5>6</hall_table__5>
    <hall_table__6>4</hall_table__6>
    <hall_table__7>-1</hall_table__7>
    <hall_sl_erpm>2000</hall_sl_erpm>
    <foc_current_kp>0.0108</foc_current_kp>
    <foc_current_ki>2.23</foc_current_ki>
    <foc_f_zv>30000</foc_f_zv>
    <foc_dt_us>0.12</foc_dt_us>
    <foc_encoder_inverted>0</foc_encoder_inverted>
    <foc_encoder_offset>180</foc_encoder_offset>
    <foc_encoder_ratio>7</foc_encoder_ratio>
    <foc_sensor_mode>2</foc_sensor_mode>
    <foc_pll_kp>2000</foc_pll_kp>
    <foc_pll_ki>30000</foc_pll_ki>
    <foc_motor_l>1.081e-05</foc_motor_l>
    <foc_motor_ld_lq_diff>2.6e-06</foc_motor_ld_lq_diff>
    <foc_motor_r>0.0022</foc_motor_r>
    <foc_motor_flux_linkage>0.018808</foc_motor_flux_linkage>
    <foc_observer_gain>2.83e+06</foc_observer_gain>
    <foc_observer_gain_slow>0.05</foc_observer_gain_slow>
    <foc_observer_offset>-1</foc_observer_offset>
    <foc_duty_dowmramp_kp>50</foc_duty_dowmramp_kp>
    <foc_duty_dowmramp_ki>1000</foc_duty_dowmramp_ki>
    <foc_start_curr_dec>1</foc_start_curr_dec>
    <foc_start_curr_dec_rpm>2500</foc_start_curr_dec_rpm>
    <foc_openloop_rpm>1500</foc_openloop_rpm>
    <foc_openloop_rpm_low>0</foc_openloop_rpm_low>
    <foc_d_gain_scale_start>0.9</foc_d_gain_scale_start>
    <foc_d_gain_scale_max_mod>0.2</foc_d_gain_scale_max_mod>
    <foc_sl_openloop_hyst>0.1</foc_sl_openloop_hyst>
    <foc_sl_openloop_time_lock>0</foc_sl_openloop_time_lock>
    <foc_sl_openloop_time_ramp>0</foc_sl_openloop_time_ramp>
    <foc_sl_openloop_time>0.1</foc_sl_openloop_time>
    <foc_sl_openloop_boost_q>3</foc_sl_openloop_boost_q>
    <foc_sl_openloop_max_q>-1</foc_sl_openloop_max_q>
    <foc_hall_table__0>255</foc_hall_table__0>
    <foc_hall_table__1>5</foc_hall_table__1>
    <foc_hall_table__2>131</foc_hall_table__2>
    <foc_hall_table__3>171</foc_hall_table__3>
    <foc_hall_table__4>60</foc_hall_table__4>
    <foc_hall_table__5>36</foc_hall_table__5>
    <foc_hall_table__6>95</foc_hall_table__6>
    <foc_hall_table__7>255</foc_hall_table__7>
    <foc_hall_interp_erpm>500</foc_hall_interp_erpm>
    <foc_sl_erpm>2000</foc_sl_erpm>
    <foc_sample_v0_v7>0</foc_sample_v0_v7>
    <foc_sample_high_current>0</foc_sample_high_current>
    <foc_sat_comp_mode>2</foc_sat_comp_mode>
    <foc_sat_comp>0</foc_sat_comp>
    <foc_temp_comp>1</foc_temp_comp>
    <foc_temp_comp_base_temp>8.8</foc_temp_comp_base_temp>
    <foc_current_filter_const>0.1</foc_current_filter_const>
    <foc_cc_decoupling>0</foc_cc_decoupling>
    <foc_observer_type>3</foc_observer_type>
    <foc_hfi_voltage_start>20</foc_hfi_voltage_start>
    <foc_hfi_voltage_run>4</foc_hfi_voltage_run>
    <foc_hfi_voltage_max>6</foc_hfi_voltage_max>
    <foc_hfi_gain>0.3</foc_hfi_gain>
    <foc_hfi_hyst>0</foc_hfi_hyst>
    <foc_sl_erpm_hfi>3000</foc_sl_erpm_hfi>
    <foc_hfi_start_samples>5</foc_hfi_start_samples>
    <foc_hfi_obs_ovr_sec>0.001</foc_hfi_obs_ovr_sec>
    <foc_hfi_samples>1</foc_hfi_samples>
    <foc_offsets_cal_on_boot>1</foc_offsets_cal_on_boot>
    <foc_offsets_current__0>2125.15</foc_offsets_current__0>
    <foc_offsets_current__1>2127.16</foc_offsets_current__1>
    <foc_offsets_current__2>2129.1</foc_offsets_current__2>
    <foc_offsets_voltage__0>-0.0037</foc_offsets_voltage__0>
    <foc_offsets_voltage__1>0.0016</foc_offsets_voltage__1>
    <foc_offsets_voltage__2>0.0021</foc_offsets_voltage__2>
    <foc_offsets_voltage_undriven__0>0</foc_offsets_voltage_undriven__0>
    <foc_offsets_voltage_undriven__1>0</foc_offsets_voltage_undriven__1>
    <foc_offsets_voltage_undriven__2>0</foc_offsets_voltage_undriven__2>
    <foc_phase_filter_enable>1</foc_phase_filter_enable>
    <foc_phase_filter_disable_fault>1</foc_phase_filter_disable_fault>
    <foc_phase_filter_max_erpm>4000</foc_phase_filter_max_erpm>
    <foc_mtpa_mode>0</foc_mtpa_mode>
    <foc_fw_current_max>0</foc_fw_current_max>
    <foc_fw_duty_start>0.9</foc_fw_duty_start>
    <foc_fw_q_current_factor>0.02</foc_fw_q_current_factor>
    <foc_fw_ramp_time>0.2</foc_fw_ramp_time>
    <foc_speed_soure>1</foc_speed_soure>
    <gpd_buffer_notify_left>200</gpd_buffer_notify_left>
    <gpd_buffer_interpol>0</gpd_buffer_interpol>
    <gpd_current_filter_const>0.1</gpd_current_filter_const>
    <gpd_current_kp>0.03</gpd_current_kp>
    <gpd_current_ki>50</gpd_current_ki>
    <sp_pid_loop_rate>5</sp_pid_loop_rate>
    <s_pid_kp>0.004</s_pid_kp>
    <s_pid_ki>0.004</s_pid_ki>
    <s_pid_kd>0.0001</s_pid_kd>
    <s_pid_kd_filter>0.2</s_pid_kd_filter>
    <s_pid_min_erpm>900</s_pid_min_erpm>
    <s_pid_allow_braking>1</s_pid_allow_braking>
    <s_pid_ramp_erpms_s>25000</s_pid_ramp_erpms_s>
    <p_pid_kp>0.025</p_pid_kp>
    <p_pid_ki>0</p_pid_ki>
    <p_pid_kd>0</p_pid_kd>
    <p_pid_offset>0</p_pid_offset>
    <p_pid_kd_proc>0.00035</p_pid_kd_proc>
    <p_pid_kd_filter>0.2</p_pid_kd_filter>
    <p_pid_ang_div>1</p_pid_ang_div>
    <p_pid_gain_dec_angle>0</p_pid_gain_dec_angle>
    <cc_startup_boost_duty>0.01</cc_startup_boost_duty>
    <cc_min_current>0.05</cc_min_current>
    <cc_gain>0.0046</cc_gain>
    <cc_ramp_step_max>0.04</cc_ramp_step_max>
    <m_fault_stop_time_ms>500</m_fault_stop_time_ms>
    <m_duty_ramp_step>0.02</m_duty_ramp_step>
    <m_current_backoff_gain>0.5</m_current_backoff_gain>
    <m_encoder_counts>8192</m_encoder_counts>
    <m_encoder_sin_amp>1</m_encoder_sin_amp>
    <m_encoder_cos_amp>1</m_encoder_cos_amp>
    <m_encoder_sin_offset>1.65</m_encoder_sin_offset>
    <m_encoder_cos_offset>1.65</m_encoder_cos_offset>
    <m_encoder_sincos_filter_constant>0.5</m_encoder_sincos_filter_constant>
    <m_encoder_sincos_phase_correction>0</m_encoder_sincos_phase_correction>
    <m_sensor_port_mode>0</m_sensor_port_mode>
    <m_invert_direction>0</m_invert_direction>
    <m_drv8301_oc_mode>0</m_drv8301_oc_mode>
    <m_drv8301_oc_adj>16</m_drv8301_oc_adj>
    <m_bldc_f_sw_min>3000</m_bldc_f_sw_min>
    <m_bldc_f_sw_max>35000</m_bldc_f_sw_max>
    <m_dc_f_sw>25000</m_dc_f_sw>
    <m_ntc_motor_beta>3380</m_ntc_motor_beta>
    <m_out_aux_mode>0</m_out_aux_mode>
    <m_motor_temp_sens_type>2</m_motor_temp_sens_type>
    <m_ptc_motor_coeff>0.61</m_ptc_motor_coeff>
    <m_ntcx_ptcx_res>10000</m_ntcx_ptcx_res>
    <m_ntcx_ptcx_temp_base>25</m_ntcx_ptcx_temp_base>
    <m_hall_extra_samples>1</m_hall_extra_samples>
    <m_batt_filter_const>55</m_batt_filter_const>
    <si_motor_poles>32</si_motor_poles>
    <si_gear_ratio>1</si_gear_ratio>
    <si_wheel_diameter>0.41</si_wheel_diameter>
    <si_battery_type>1</si_battery_type>
    <si_battery_cells>24</si_battery_cells>
    <si_battery_ah>30</si_battery_ah>
    <si_motor_nl_current>1</si_motor_nl_current>
    <motor_brand>Unnamed</motor_brand>
    <motor_model>Not Specified</motor_model>
    <motor_weight>0</motor_weight>
    <motor_sensor_type>0</motor_sensor_type>
    <motor_description>&lt;!DOCTYPE HTML PUBLIC &quot;-//W3C//DTD HTML 4.0//EN&quot; &quot;http://www.w3.org/TR/REC-html40/strict.dtd&quot;&gt;
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

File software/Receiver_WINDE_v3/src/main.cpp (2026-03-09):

#include <Arduino.h>
#include <RadioLib.h>
#include "LiPoCheck.h"    //to calculate battery % based on cell Voltage
#include <Pangodream_18650_CL.h>
#include <SPI.h>
#include <Wire.h>  
#include "SSD1306.h"
#include <rom/rtc.h>
#include <Button2.h>
#include <VescUart.h>
#include "common.h"
#include <EEPROM.h>

// /*
//  * receiver
//  * receives target pull value from lora link
//  * sends acknowlegement on lora with current parameters
//  * writes target pull with PWM signal to vesc
//  * reads current parameters (tachometer, battery %, motor temp) with UART from vesc, based on (https://github.com/SolidGeek/VescUart/)
//  * 
//  */


#define EEPROM_SIZE 20
#define EEPROM_STARTUP_COUNTER 0
#define EEPROM_DEVICE_ID 0
#define EEPROM_MAX_PULL  1

int rssi = 0;
float snr = 0;
bool debug = false;
char txtOut[40];
char serialIn[20];
int serialInBufferPos;
int serialReceiverWaiting;
LoraTxMessage loraTxMsg;
LoraRxMessage loraRxMsg;

#define LED_ONBOARD 35
SX1262 radio = new Module(8, 14, 12, 13);  
 
bool loraRxFlag;
void radioInterrupt(void){
  int irReason = radio.getIrqFlags();
  if(debug){
    Serial.printf("IRQ fired: 0x%X\r\n", irReason);
  }
  if(debug) Serial.printf("Lora INT: %d\r\n", irReason);
  if(irReason == 0x12){ // 18 is RX IRQ
    //Serial.println("Set Flag");
    loraRxFlag = true;
  }
  else{
    if((irReason != 0x12)&&(irReason != 0x01)){
      Serial.printf("IRQ: 0x%X -> Delete IRQ\r\n", irReason);
      radio.clearIrq(RADIOLIB_SX126X_IRQ_ALL);
    }
  }
}

void getLoraState(void){
  uint16_t irq = radio.getIrqFlags();
  Serial.printf("RL IRQ Status: 0x%X\r\n", irq);
}


void lora_init(void){
  Serial.println("Lora Receiver startet...");
  int state = radio.begin(866.5, 125.0, 8, 5, 0x12, 14);
  if (state != RADIOLIB_ERR_NONE) {
    Serial.print("Init fehlgeschlagen: ");
    Serial.println(state);
  }

  radio.setCRC(true);
  radio.setDio1Action(radioInterrupt);
  radio.startReceive();
  Serial.println("Empfänger bereit.");
}

//   // // Pins Rotary Encoder
//   // #define ROTARY_SW  2
//   // #define ROTARY_A   3
//   // #define ROTARY_B   4

//   // // Buttons for state machine control
//   // #define BUTTON_UP    5 // up
//   // #define BUTTON_DOWN  6 // down

//   // Pins OLED Display

  #define OLED_SDA  17
  #define OLED_SCL  18
  #define OLED_RST  21 // only in Heltec mode used

  // No battery used in receiver
  #define BAT_AN_IN  1
  #define BAT_EN_AN 37 // Enable ADC divider for meassure BAT voltage

  // Define sonstiger Pins
  // LED's zur Statusausgabe, grün leuchtet wenn an, rot blitzt bei LoraRX auf
  //Battery Voltage IO 7 -> Wind direction
  // #define WindInAnalog  7

  #define VESC_RX  38    //connect to TX on Vesc
  #define VESC_TX  39    //connect to RX on Vesc

  // #define Cutter_Out 40 // up
  // #define LED_RT 41 // down
  // Pins Rotary Encoder -> Funktionen:
  // - Seil manuell einziehen (Zug mehr / weniger über drehen, bei Push SoftBreak)

  // #define WARN_LIGHT_OUT 42 
  // #define FAN_OUT   45

  #define PWM_PIN_OUT  46 //Define Digital PIN

// //vesc battery number of cells
static int numberOfCells = 24; // LiFePo pack
// static int myMaxPull = 75;  // 0 - 127 [kg], must be scaled with VESC ppm settings

SSD1306 display(0x3C, OLED_SDA, OLED_SCL);

//Using VescUart librarie to read from Vesc (https://github.com/SolidGeek/VescUart/)
// Uart old
// #define VESC_RX  14    //connect to TX on Vesc
// #define VESC_TX  2    //connect to RX on Vesc
// Uart new

VescUart vescUART;

// PWM signal to vesc
#define PWM_TIME_0      950.0    //PWM time in ms for 0% , PWM below will be ignored!! need XXX.0!!!
#define PWM_TIME_100    2000.0   //PWM time in ms for 100%, PWM above will be ignored!!

static int loopStep = 0;
static uint8_t activeTxId = 0;

int smoothStep = 0;    // used to smooth pull changes
int hardBrake = -20;  //-20 kg
int softBrake = -7;  //-7 kg
int defaultPull = 7;  //7 kg
int prePullScale = 20;      //20 % of myMaxPull
int takeOffPullScale = 50;  //50 % of myMaxPull
int fullPullScale = 80;     //80 % of myMaxPull
int strongPullScale = 100;  //100 % of myMaxPull

int currentId = 0;
int currentState = -1;
// pull value send to VESC --> default soft brake
// defined as int to allow smooth changes without overrun
int currentPull = softBrake;     // active range -127 to 127
int8_t targetPullValue = 0;    // received from lora transmitter or rewinding winch mode
int rotaryPull = 0; // set by rotary and reset to 0 if lora link != -1

uint8_t vescBattery = 0;
uint8_t vescTempMotor = 0;
unsigned long lastTxLoraMessageMillis = 0;
unsigned long previousTxLoraMessageMillis = 0;
unsigned long lastRxLoraMessageMillis = 0;
unsigned long previousRxLoraMessageMillis = 0;
uint32_t  pwmReadTimeValue = 0;
uint32_t  pwmWriteTimeValue = 0;
unsigned long lastWritePWMMillis = 0;
unsigned int loraErrorCount = 0;
unsigned long loraErrorMillis = 0;


int encValue = 0;
unsigned char encIn, encInAlt, enc0, enc1, enc2;
void rotaryInterrupt(void){
  // encIn = digitalRead(ROTARY_A)+digitalRead(ROTARY_B)*2;
  if(encInAlt != encIn){
    encInAlt = encIn;
    enc0 = enc1;
    enc1 = enc2;
    enc2 = encIn;
    if((enc0 == 0)&&(enc1 == 1)&&(enc2 == 3)){
      encValue -= 1;
    }
    if((enc0 == 3)&&(enc1 == 2)&&(enc2 == 0)){
      encValue -= 1;
    }
    if((enc0 == 0)&&(enc1 == 2)&&(enc2 == 3)){
      encValue += 1;
    }
    if((enc0 == 3)&&(enc1 == 1)&&(enc2 == 0)){
      encValue += 1;
    }
  }
}

void encoderInit(void){
  // pinMode(ROTARY_A, INPUT_PULLUP);
  // pinMode(ROTARY_B, INPUT_PULLUP);
  // attachInterrupt(ROTARY_A, rotaryInterrupt, CHANGE);
  // attachInterrupt(ROTARY_B, rotaryInterrupt, CHANGE);
}

void pulseOut(int pin, int us)
{
   digitalWrite(pin, HIGH);
   us = max(us - 20, 1);  //biase caused by digital write/read
   delayMicroseconds(us);
   digitalWrite(pin, LOW);
}

void pullByUart(int current){
  if(current > 0){
    vescUART.setCurrent(current);
  }
  else{
    vescUART.setBrakeCurrent(current);
  }
}

#define WIND_VALUE_OFFSET 112
uint8_t get_wind_direction(void){
  // Wind direction from potentiometer value 0 ... 4096
  // output 7 Bit max, value 0 ... 36 is direction with factor 10 degree
  uint16_t anValue = 0;//analogRead(WindInAnalog);
  // if(anValue < WIND_VALUE_OFFSET){
  //   anValue = 4095 - WIND_VALUE_OFFSET; 
  // }
  // else{
  //   anValue -= WIND_VALUE_OFFSET;
  // }
  // anValue /= 112;
  // Serial.print("AN Wind: ");
  // Serial.println(anValue);
  return anValue;
}
uint8_t startupCounter = 0;

uint32_t nextSendTime;
#define BOOT_Pin 0
uint8_t bootPinIn, bootPinInAlt;
#define VEXT_CTL 36
void setup() {
  EEPROM.begin(EEPROM_SIZE);
  startupCounter = EEPROM.read(EEPROM_STARTUP_COUNTER)+1;
  EEPROM.write(EEPROM_STARTUP_COUNTER, startupCounter);
  EEPROM.commit();
  pinMode(LED_ONBOARD, OUTPUT);
  digitalWrite(LED_ONBOARD, 0);

  #ifdef VEXT_CTL
    pinMode(VEXT_CTL, OUTPUT);
    digitalWrite(VEXT_CTL, 0);
  #endif

  #ifdef OLED_RST
    delay(10);
    pinMode(OLED_RST, OUTPUT);
    digitalWrite(OLED_RST, 1);
    delay(100);
    digitalWrite(OLED_RST, 0);
    delay(100);
    digitalWrite(OLED_RST, 1);
  #endif

  pinMode(BOOT_Pin, INPUT_PULLUP);
  // pinMode(Cutter_Out, OUTPUT);
  // digitalWrite(Cutter_Out, 0);
  // pinMode(LED_RT, OUTPUT);
  // digitalWrite(LED_RT, 1);
  // pinMode(WindInAnalog, ANALOG);
  Serial.begin(115200);

  encoderInit();
  //Setup UART port for Vesc communication
  Serial1.begin(115200, SERIAL_8N1, VESC_RX, VESC_TX);
  vescUART.setSerialPort(&Serial1);
  
  //lora init
  lora_init();

  // display init
  delay(500);
  display.init();
  display.setBrightness(200);
  display.flipScreenVertically();  

  //PWM Pins
  //pinMode(PWM_PIN_IN, INPUT);
  pinMode(PWM_PIN_OUT, OUTPUT);
  
  display.clear();
  display.setTextAlignment(TEXT_ALIGN_LEFT);
  display.setFont(ArialMT_Plain_10);
  Serial.printf("Starting Receiver \n");
  display.drawString(0, 0, "Starting Receiver");
  display.display();
  // digitalWrite(LED_RT, 0);
  nextSendTime = millis();

  Serial.print("Startup number ");
  Serial.print(startupCounter);
  Serial.println(" done.");
}

uint32_t sendCycle =0;
uint32_t now, lastSend, lastRead;
uint16_t counter_send;

uint32_t loraRxCnt = 0, loraTxCnt = 0;
uint32_t nextTime = 0;
uint8_t rxData[10];
void loop() {
 if (true) {
    // screen
    loopStep++;
    if (loopStep % 10 == 0) { // Display aktualisieren
      display.clear();
      display.setTextAlignment(TEXT_ALIGN_LEFT);
      display.setFont(ArialMT_Plain_10);  //10, 16, 24
      //display.drawString(0, 0, currentId + String("-RX: (") + BL.getBatteryChargeLevel() + "%, " + rssi + "dBm, " + snr + ")");
      display.drawString(0, 0, currentId + String("-RX: (")+ rssi + "dBm, " + snr + ")");
      display.setFont(ArialMT_Plain_24);  //10, 16, 24
      if (currentState == -7){
          display.drawString(0, 11, "Cutting");  
          // digitalWrite(Cutter_Out, 1);
      }
      else if (currentState > 0){
          // digitalWrite(Cutter_Out, 0);
          display.drawString(0, 11, String("P ") + currentState + ": (" + currentPull + "kg)");  
      } else {
          // digitalWrite(Cutter_Out, 0);
          display.drawString(0, 11, String("B ") + currentState + ": (" + currentPull + "kg)");    
      }
      display.setFont(ArialMT_Plain_10);  //10, 16, 24
      //display.drawString(0, 36, String("Error / Uptime{min}: ") + loraErrorCount + " / " + millis()/60000);
      display.drawString(0, 36, String("B: ") + vescBattery + "%, M: " + vescTempMotor + "C" +" R"+encValue + " UP "+startupCounter); 
      display.drawString(0, 48, String("TX / RX: ") + loraRxCnt + " / " + loraTxCnt);
      display.display();
    }
    if(loraRxFlag){
      loraRxFlag = false;
      int state = radio.readData(rxData, sizeof(loraRxMsg.byte));
      if (state != RADIOLIB_ERR_NONE) {
        Serial.println("Lora Rx Error");
      }
      else{
        if(rxData[0]== 0xCB){
          loraRxCnt ++;
          digitalWrite(LED_ONBOARD,1);
          rssi = radio.getRSSI();
          snr = radio.getSNR();
          memcpy(loraRxMsg.byte, rxData, sizeof(loraRxMsg.byte));
          if(debug){
            Serial.print("Lora Rx: ");
            for(int z=0;z<sizeof(loraRxMsg.byte);z++){
              Serial.printf("0x%02X ", loraRxMsg.byte[z]);
            }
            Serial.println("");
          }
            // Serial.print("Data from Lora: ");
            // Serial.printf("ID: %d State: %d PullValue: %d", loraRxMsg.id, loraRxMsg.currentState, loraRxMsg.pullValue);    
            // Serial.println();
            // digitalWrite(LED_RT, 1);
          if (millis() > lastTxLoraMessageMillis + 5000){
            activeTxId = loraRxMsg.id;
          }
          // The admin id 0 can allways take over 
          if (loraRxMsg.id == 0){
            activeTxId = loraRxMsg.id;
          }
          if ((loraRxMsg.id == activeTxId) && (loraRxMsg.pullValue == loraRxMsg.pullValueBackup)) {
              targetPullValue = loraRxMsg.pullValue;
              currentId = loraRxMsg.id;
              currentState = loraRxMsg.currentState;
              previousTxLoraMessageMillis = lastTxLoraMessageMillis;  // remember time of previous paket
              lastTxLoraMessageMillis = millis();
              //Serial.printf("Value received: %d, RSSI: %d: , SNR: %d\n", loraRxMsg.pullValue, rssi, snr);
              
              // send ackn after receiving a value
              // delay(10);
              loraTxMsg.startframe = 0xBC;
              loraTxMsg.pullValue = currentPull;
              loraTxMsg.tachometer = abs(vescUART.data.tachometer)/725;     // %100 --> in m, %10 --> to use only one byte for up to 2550m line lenght
              //Serial.printf("Tacho: %d\r\n", vescUART.data.tachometer);
              // alternate vescBatteryPercentage and vescTempMotor value on lora link to reduce packet size
              if(loraTxMsg.dutyCycleOrWindDirection == 0){
                loraTxMsg.dutyCycleOrWindDirection = 1;
                loraTxMsg.dutyCycleOrWindDirektionValue = abs(vescUART.data.dutyCycleNow * 100);     //in %
              }
              else{ // Wind direction max value = 127, real 360 degree
                    // direction will be transmitted by faktor 10, 0...36 
                loraTxMsg.dutyCycleOrWindDirection = 0;
                loraTxMsg.dutyCycleOrWindDirektionValue = get_wind_direction();
              }
             
              if (loraTxMsg.vescBatteryOrTempMotor == 0){
                loraTxMsg.vescBatteryOrTempMotor = 1;
                loraTxMsg.vescBatteryOrTempMotorValue = vescBattery;
              } else {
                loraTxMsg.vescBatteryOrTempMotor = 0;
                loraTxMsg.vescBatteryOrTempMotorValue = vescTempMotor;
              }
              // digitalWrite(LED_RT, 0);
              delay(10);
              digitalWrite(LED_ONBOARD, 0);
              int txState = radio.transmit(loraTxMsg.byte, sizeof(loraTxMsg.byte));
              radio.startReceive();
              
              if (txState == RADIOLIB_ERR_NONE) {
                loraTxCnt ++;
                if(debug){
                  Serial.print("Lora Tx: ");
                  for(int z=0;z<sizeof(loraTxMsg.byte);z++){
                    Serial.printf("0x%02X ", loraTxMsg.byte[z]);
                  }
                  Serial.println("");
                  Serial.printf("sending pull value %d: \r\n", targetPullValue);
                }
                lastTxLoraMessageMillis = millis();  
              } 
              else {
                Serial.printf("Lora send error: 0x%X\r\n", txState);
              }       
        }
    }
      }
    }
    // if no lora message for more then 1,5s --> show error on screen + acustic
    if (millis() > lastTxLoraMessageMillis + 1500 ) {
          //TODO acustic information
          //TODO  red disply
          display.clear();
          display.display();
          // log connection error
          if (millis() > loraErrorMillis + 5000) {
              loraErrorMillis = millis();
              loraErrorCount = loraErrorCount + 1;
          }
    }
    // Failsafe only when pull was active
    if (currentState >= 1) {
          // no packet for 1,5s --> failsave
          if (millis() > lastTxLoraMessageMillis + 1500 ) {
                // A) keep default pull if connection issue during pull for up to 10 seconds
                if (millis() < lastTxLoraMessageMillis + 20000) {
                  targetPullValue = defaultPull;   // default pull
                  currentState = 1;
                } else {
                // B) go to soft brake afterwards
                  targetPullValue = softBrake;     // soft brake
                  currentState = -1;
                }
          }
    }
    if (currentState == -7){
      Serial.println("CUT line!!!");
    }
  }
 
 else {
      // rewinding winch mode
      // screen
      if (loopStep % 10 == 0) {
        display.clear();
        display.setTextAlignment(TEXT_ALIGN_LEFT);
        display.setFont(ArialMT_Plain_10);  //10, 16, 24
        display.drawString(0, 0, "rewinding winch mode");
        display.setFont(ArialMT_Plain_24);  //10, 16, 24
        display.drawString(0, 14, String(targetPullValue) + "/" + currentPull + "kg");
        display.display();
      }

      // small pull value on pull out
      // higher pull value on pull in
      if (vescUART.data.dutyCycleNow > 0.02){
        targetPullValue = 10;
      } else if (vescUART.data.dutyCycleNow < -0.02){
        targetPullValue = 17;
      } else {
        targetPullValue = -5; // no line movement --> soft brake
      }
      // ??? TODO higher pull value on fast pull out to avoid drum overshoot on line disconection ???
      
 }  // end rewind winch mode

      // auto line stop
      // (smouth to avoid line issues on main winch with rewinding winch)
      // tachometer > 2 --> avoid autostop when no tachometer values are read from uart (--> 0)
      if (vescUART.data.tachometer > 2 && vescUART.data.tachometer < 40) {
          if (targetPullValue > defaultPull){
              targetPullValue = defaultPull;
          }
          if (vescUART.data.tachometer < 20) {
              targetPullValue = softBrake;
          }
          if (vescUART.data.tachometer < 10) {
              targetPullValue = hardBrake;
          }
          // Serial.println("Autostop active, target pull value:");
          // Serial.println(targetPullValue);
      }
 
      // smooth changes
      // if brake --> immediately active
      if (targetPullValue < 0 ){
          currentPull = targetPullValue;
      } else {   
          // change rate e.g. max. 50 kg / second
          //reduce pull
          if (currentPull > targetPullValue) {
              smoothStep = 90 * (millis() - lastWritePWMMillis) / 1000;
              if ((currentPull - smoothStep) > targetPullValue)   //avoid overshooting
                  currentPull = currentPull - smoothStep;
              else
                  currentPull = targetPullValue;
          //increase pull
          } else if (currentPull < targetPullValue) {
              smoothStep = 65 * (millis() - lastWritePWMMillis) / 1000;
              if ((currentPull + smoothStep) < targetPullValue)   //avoid overshooting
                  currentPull = currentPull + smoothStep;
              else
                  currentPull = targetPullValue;
          }
          //Serial.println(currentPull);
          //avoid overrun
          if (currentPull < -127)
            currentPull = -127;
          if (currentPull > 127)
            currentPull = 127;
      }
      delay(10);
      //calculate PWM time for VESC
      // write PWM signal to VESC
      // pwmWriteTimeVal = (-127 ... 127 + 127)*(2000 - 950) / 254 + 950
                          // -20 = 1392 
                          // -7  = 1446
                          //  0  = 1475
                          //  7  = 1503
                          //  20 = 1557
                          // 90  = 1847 // max. für Solo
                          // 127 = 2000 // max. für Tandem
      // PWM to current:
      // PWM range from 1.480 to 2.000
      // 520 mV for pull range 0 ... 310 A
      // 90 kg -> 0x372 V -> 222 A 
      pwmWriteTimeValue = (currentPull + 127) * (PWM_TIME_100 - PWM_TIME_0) / 254 + PWM_TIME_0;   
      // pulseOut ist eine Soft-PWM, HardPWM auch möglich?   
      pulseOut(PWM_PIN_OUT, pwmWriteTimeValue);
      lastWritePWMMillis = millis();

      if (currentState != -1){
        encValue = 0;
      } else{
        pullByUart(encValue);
        // Serial.printf("Pull value: %d\r\n", encValue);
      }
      // Turn on warning light if in pull mode
      // if(currentState > 0){
      //   digitalWrite(WARN_LIGHT_OUT, 1);
      // } else{
      //   digitalWrite(WARN_LIGHT_OUT, 0);
      // }

      delay(10);    //RC PWM usually has a signal every 20ms (50 Hz)

      
      //read actual Vesc values from uart
      if (loopStep % 10 == 0) {
        if (vescUART.getVescValues()) {
          vescBattery = CapCheckPerc(vescUART.data.inpVoltage, numberOfCells);    // vesc battery in %
          vescTempMotor = vescUART.data.tempMotor;                                // motor temp in C   

          // Turn on fan if Mosfet temp rises above 50 °C
          // if(vescUART.data.tempMosfet > 50){
          //   digitalWrite(FAN_OUT, 1);
          // } else{
          //   digitalWrite(FAN_OUT, 0);
          // }

        } else
        {
          //TODO send notification to lora
          //measuredVescVal.tachometer = 0;
          // Serial.println("Failed to get data from VESC!");
        }
         
        //  if(digitalRead(ROTARY_SW)==0){
        //   encValue = 0;
        //  }

        // sprintf(txtOut,"Rotary pull: %d", encValue);
        //Serial.println(txtOut);
      }

      bootPinIn = digitalRead(BOOT_Pin);
      if((bootPinIn==0)&&(bootPinInAlt != 0)){
        Serial.println("Boot Switch !!!");
      }
      bootPinInAlt = bootPinIn;

      char rcChar; 
      if(Serial.available()){
        
        Serial.read(&rcChar, 1);
        Serial.printf("Got char %c ", rcChar);
        if(rcChar == 'i'){ // info request
          getLoraState();
        }
        if(rcChar == 'd'){
          if(debug){
            debug = false;
            Serial.println("DEBUG off");
          }
          else{
            debug = true;
            Serial.println("DEBUG on");
          }
        }
        if(rcChar == 'r'){
          serialInBufferPos = 0;
          serialIn[serialInBufferPos++] =rcChar; 
          serialReceiverWaiting = 1;
        }
        else if(serialReceiverWaiting){
          serialIn[serialInBufferPos++] =rcChar; 
        }
        if(serialInBufferPos >= 3){
          serialReceiverWaiting = 0;
          serialIn[3]= 0;
          if(strcmp("rst", serialIn)==0){
            Serial.println("got reset command!");
            EEPROM.write(EEPROM_STARTUP_COUNTER, 0);
            EEPROM.commit();
          }
        }
      }
    }

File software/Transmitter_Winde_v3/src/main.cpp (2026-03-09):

/*
Erweiterung der Funktionen: 
 - Rotary-Encoder um in Setup-Menü die max. Zugkraft einstellen zu können
  -> nur möglich wenn im Idle-Mode

 - Taster für Aktivierung Kapp-System
    -> Longpress (>1s) um Fehlbedienung zu vermeiden
*/
/*
 * 
 * transmitter
 * sends current state (pull value)
 * receives acknowlegement with current parameters
 * 
 */
// communication is locked to a specific transmitter for 5 seconds after his last message
// admin ID 0 can allays take over communication
// ID and max pull can be adjustet in setup, push rotary when switching on to enter setup
static int myID = 1;    // set to your desired transmitter id!!! [unique number from 1 - 15] 
static int myMaxPull = 85;  // 0 - 127 [kg], must be scaled with VESC ppm settings
// with Setup Encoder you can set myId and myMaxPull by rotary encoder

#include <Arduino.h>
#include <RadioLib.h>
#include "common.h"
#include "Button2.h"
#include <SPI.h>
#include <Wire.h> 
#include <SSD1306.h>  
#include "Battery18650Stats.h"
#include <rom/rtc.h>
#include <EEPROM.h>
#include <WiFi.h>

#define USE_ESPNOW
#ifdef USE_ESPNOW
#include <esp_now.h>

#define WIND_DIR_VAL    0
#define DUTY_CYCLE_VAL  1
#define MOTOR_TEMP_VAL  0
#define BAT_SOC_VAL     1

uint8_t espnowTarget[]={0x7C, 0xDF, 0xA1, 0xED, 0x63, 0x18};
typedef struct struct_message {
  int state;
  int kgSoll;
  int kgIst;
  int lineLength;
  int windDirection;
  bool cut;
  bool timeout;
} t_RC_Winch;

t_RC_Winch rcWinch;
esp_now_peer_info_t peerInfo;
void OnDataSent(const uint8_t *mac_addr, esp_now_send_status_t status) {
  Serial.print("\r\nLast Packet Send Status:\t");
  Serial.println(status == ESP_NOW_SEND_SUCCESS ? "Delivery Success" : "Delivery Fail");
}
#endif


#define EEPROM_SIZE 20
#define EEPROM_DEVICE_ID 0
#define EEPROM_MAX_PULL  1
#define EEPROM_DEF_PULL  2 // Default-Pull einstellbar machen

int rssi = 0;
float snr = 0;
String packSize = "--";
String packet;
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

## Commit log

2023-12-26 prepared for line cutter
    [ESP32MB_V12.kicad_pcb, ESP32MB_V12.kicad_sch, ESP32_Pinning_Transmitter.xlsx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]
2024-02-22 Firmware FOC G300 mit Autostop hinzu
    [Winde_Trommelblatt.FCStd, vesc_app_config.xml, vesc_app_config_JM.xml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]
2024-06-03 Added CockpitDisplay to project
    [DisplayCaseBack.step]
2024-06-03 sorted vesc folder
    [vesc_app_config.xml, vesc_app_config_JM.xml, vesc_motor_config_12kw_260_V4.xml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]
2024-06-18 Changed Lora to 866.5 MHz and set SF to 9, changed RadioLib receiver to interrupt
2024-07-21 added wind direction sensor to receiver
    [ESP32MB_V12.kicad_sch]
2024-07-21 updated vesc config
    [2024_07_20_vesc_app_config_JM.xml, 2024_07_20_vesc_motor_config_12kw_273.xml]
2024-09-04 some improvements and cad data addad
    [2024_07_12_vesc_app_config_JM.xml, 2024_07_12_vesc_motor_config_12kw_273.xml, 2024_08_18_vesc_motor_config_12kw_273_300A.xml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]
2025-03-18 added pictures
    [ESP32_Pinning_Transmitter.xlsx]
2026-02-27 Update Transmitter_v3 mit powerManager zum Laden
    [2024_07_12_vesc_app_config_JM.xml, 2024_07_12_vesc_motor_config_12kw_273.xml, 2024_07_20_vesc_app_config_JM.xml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]
2026-03-06 Transmitter und Receiver auf Heltec Lora v3 angepasst. Lora stabil mit Interrupt, Reichweite rund 1,3km. 400ms Cycle läuft. Anpassung der restlichen SW steht noch aus
2026-03-07 Transmitter code working after redesign
    [main.cpp]
2026-03-09 Receiver fully working after adjusting interrupt behaviour
2026-03-09 IRQ error handling extented
    [Kreuzspindel_kurz.step]
